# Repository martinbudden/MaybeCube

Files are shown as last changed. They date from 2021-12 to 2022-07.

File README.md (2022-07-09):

# MaybeCube

The **MaybeCube** is a fully-featured, rigid, high speed, and affordable CoreXY 3D printer with a linear rails motion system.

It can be built in a variety of sizes: the standard size is the MC350, which has external dimensions of approximately
405mm by 475mm by 415mm and a build volume of approximately 225mm x 225mm x 200mm.

The self-sourcing BOM cost of the MC300 variant is approximately £430 with a genuine E3D hotend (or about £400 with a generic
E3D compatible hotend), this does not include the cost of filament for printing parts, see [spreadsheet](documents/BOM_MC300.ods).
The MC350 variant is slightly more expensive.

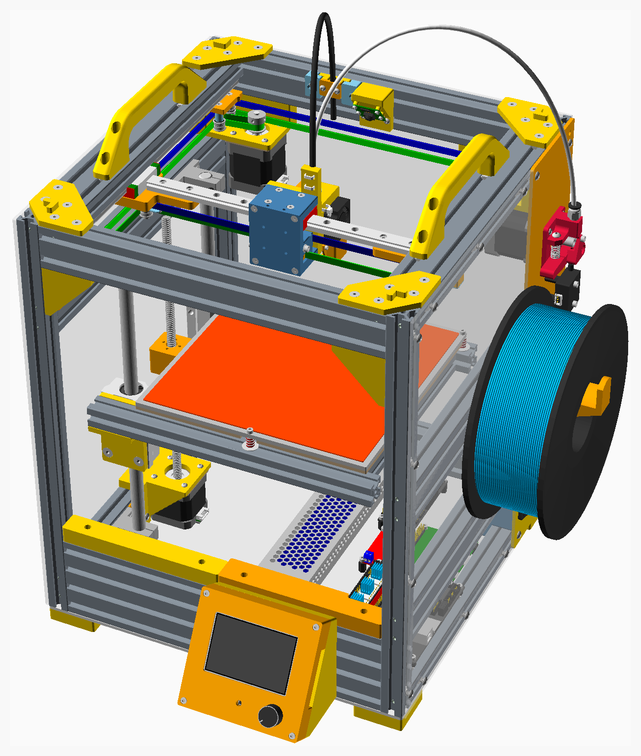
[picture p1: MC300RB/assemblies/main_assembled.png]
Main Assembly


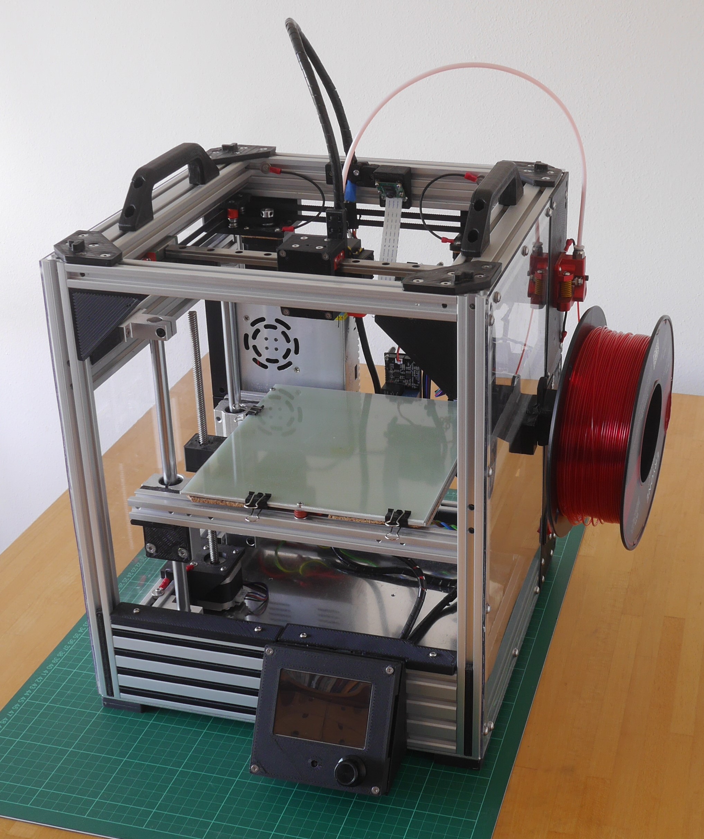
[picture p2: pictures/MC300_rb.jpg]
MaybeCube300


## Assembly instructions

The "standard" size is the MC350 variant. I have built the MC300 variant for two reasons: to test sizing (if the components
fit in the MC300 variant, then they will fit in larger variants); and because I had a quantity of 300mm extrusion and the
right size heated bed from an earlier project.

The assembly instructions and the BOM (parts list) for the MC300 variant are [here](https://github.com/martinbudden/MaybeCube/blob/main/MC300RB/readme.md).

The assembly instructions and the BOM for the MC350 variant are [here](https://github.com/martinbudden/MaybeCube/blob/main/MC350/readme.md).

Please read all the build instructions before you begin assembly.

The STL files are on [thingiverse](https://www.thingiverse.com/thing:4912095).

The assembly of the different MC300 and MC350 variants is essentially the same, the main differences are in the printbed.
Larger variants have a larger printbed and to support this can optionally have either Z-rods on both sides of the printbed,
or a 3-point kinematic bed.

If you would like to build a smaller printer, you may be interested in the MaybeCube's smaller sibling, the [BabyCube](https://github.com/martinbudden/BabyCube).

## Design Goals

1. **Create a high quality engineered 3D printer capable of producing high quality prints**
2. **Make the MaybeCube more easily usable in home environment (as opposed to garage or workshop)**
     * try and make it easy to transport and store the MaybeCube, so:
     * integrated design, everything is enclosed within the printer's frame with. This includes the motors,
       the motion system, the power supply, and the circuit boards. The only exceptions are the spool
       holder, which can be removed for transport and storage, and the extruder.
     * include base plate so underside of printer is not exposed
     * all protrusions from frame (filament spool, extruder, power connector) are on the right hand side to minimise desk
       clutter and allow the back of the MaybeCube to be pushed right against a wall
     * all protrusions from the frame can be easily removed for storage
     * clean wiring - route wiring in extrusion channels where possible and minimise exposed wiring
3. **Improve ease of assembly**
     * Use internal blind joints on the frame
     * printed parts designed so that bolts are accessible and can be tightened when frame fully assembled (that is bolt
       holes are not blocked by other parts when assembled)
     * divide the main assembly into a number of independent sub-assemblies.
     * where possible printed parts push up right against frame and so "auto-align"
     * facilitate building in different size variants
4. **Use linear rails for the x and y axes**
     * linear rails are now not much more expensive than linear rods
     * linear rails make design and assembly easier, reducing the need for custom printed parts
     * linear rods are used for the z-axis, since linear rails offer no advantage here
5. **Maximise frame rigidity**
     * one of my goals is to experiment with high print speeds. A highly rigid frame allows higher acceleration settings
     * use 2040 aluminium extrusion, corner joints are about 4 times more rigid than 2020 corner joints and 2-3 times more
       rigid than 3030 corner joints
6. **Maximise build volume for selected extrusion lengths**
     * Z-axis assembly is on the left side of MaybeCube. This means the Z-axis assembly does not impede travel in the Y direction
     * The printhead is quite compact, so does not significantly restrict travel in the X and Y directions
7. **Enable a fully enclosed print volume**
     * The cubic shape makes enclosure straightforward.
     * A panel can be used to isolate the electronics and stepper motors from the build volume
     * A slide-in front panel can be added
     * A top enclosure can be placed on the frame
8. **Try and keep the costs down**
     * the aim is not to be as cheap as possible, but rather to avoid unnecessary costs
     * use standard extrusions lengths, as far as possible, so no custom cutting is required
9. **Facilitate customisation and experimentation**
     * Open source design
     * Parametric design in OpenSCAD
     * The open design of the frame and the easy accessibility of parts means the MaybeCube is fairly easy to customise -
       most parts can be changed without the need to disassemble large parts of the frame
     * The design of the X_Carriage means it is easy to customise to support different hotends and extruders
     * Support other printhead systems, including EVA, XChange, and, in principle, the Jubilee and E3D toolchangers
     * The independence of the XY motion system and the Z motion system means that in principle the Z motion system could
       be replaced (with, say, an auto-tramming 3-point leveling system)

## Variations

The canonical form is the MC350 variant.

variant | Extrusion lengths | Rail/rod lengths | Approx Build Volume | Bed Size   | Exterior Dimensions
------- | ----------------- | ---------------- | ------------------- | ---------- | -------------------
MC250   | x250 y250 z350    | x200 y250 z250   | concept variant     | 180mm      | 290 x 290 x 350
MC300   | x300 y300 z400    | x250 y300 z300   | 185 x 185 x 200     | 214mm      | 340 x 340 x 400
MC350   | x350 y350 y400    | x300 y350 z300   | 225 x 225 x 200     | 235mm      | 390 x 390 x 400
MC400   | x400 y400 y500    | x350 y400 z400   | 275 x 275 x 300     | 310mm      | 440 x 440 x 450

## Comparisons

The following table compares the sizes and build volumes of various CoreXY 3D printers.

Printer           | EType | Extrusion lengths | Build Volume     | Exterior Dimensions
------------------|------ | ----------------- | ---------------- | -------------------
MC300             | 2040  | 300 x 300 x 400   | 185 x 185 x 200  | 340 x 340 x 420
MC350             | 2040  | 350 x 350 x 400   | 225 x 225 x 200  | 390 x 390 x 420
MC400             | 2040  | 400 x 400 x 500   | 275 x 275 x 300  | 440 x 440 x 520
MC450             | 2040  | 450 x 450 x 550   | 325 x 325 x 350  | 490 x 490 x 570
[BLV MGN Cube](https://www.blvprojects.com/blv-mgn-cube-3d-printer) | 2040 | 496 x 496 x 560 | 300 x 300 x 365 | 576 x 536 x 560
[Denali 200](https://github.com/Annex-Engineering/Denali) | 2020 | 320 x 320 x 590 | 200 x 200 x 200 | 380 x 380 x 620 (est)
Denali 250 | 2020 | 370 x 370 x 590 | 250 x 250 x 200 | 430 x 430 x 620 (est)
Denali 350 | 2020 | 470 x 470 x 690 | 350 x 350 x 300 | 530 x 530 x 720 (est)
[E3D ToolChanger](https://e3d-online.com/pages/toolchanger) | 2040 | Z: 500 |  200 x 300 x 300  | 530 x 505 x 500
[FuseBox3](https://github.com/alexyu132/fusebox3) | 2020 | 310 x 332 x 407 | 235 x 235 x 235 | 350 x 372 x 427
[HyperCube](https://www.thingiverse.com/thing:1752766) | 2020 | 340 x 303 x 350  | 200 x 200 x 155  | 380 x 343 x 350
[HEVO](https://www.thingiverse.com/thing:2254103) | 3030 | 420 x 410 x 500 | 300 x 300 x 300 | 480 x 470 x 500
[HevORT 315](https://miragec79.github.io/HevORT/) | 3030 | 410 x 420 x 880 | 315 x 315 x 340 | 640 x 480 x 890 (est)
HevORT 415                                        | 3030 | 510 x 520 x 980 | 415 x 415 x 440 | 740 x 480 x 990 (est)
[Jubilee](https://www.jubilee3d.com/index.php?title=Main_Page) | 2020 | 409 x 604 x 430 | 300 x 300 x 300 | 476 x 604 x 558
[RatRig V-Core3 300](https://v-core.ratrig.com/#customization) | 3030 | 440 x 505 x 510 | 300 x 300 x 300  | 518 x 583 x 560
RatRig V-Core3 400 | 3030 | 540 x 605 x 610 | 400 x 400 x 400  | 618 x 683 x 660
RatRig V-Core3 500 | 3030 | 640 x 705 x 710 | 500 x 500 x 500  | 718 x 783 x 760
[RailCore II 300ZL](https://railcore.org/) | 1515 | 400 x 370 x 360 | 250 x 250 x 280 | 522 x 445 x 496
RailCore II 300ZL  | 1515 | 460 x 425 x 445 | 300 x 300 x 330 | 572 x 495 x 546
RailCore II 300ZLT | 1515 | 460 x 425 x 745 | 300 x 300 x 600 | 572 x 495 x 830
[SimpleCore 200](https://github.com/rolohaun/SimpleCore) | 2020 | 350 x 350 x 450 | 200 x 200 x 180 | 390 x 390 x 390 (est)
SimpleCore 300 | 2020 | 500 x 500 x 500 | 330 x 330 x 230 | 540 x 540 x 540 (est)
[SnakeOil XY 180](https://github.com/ChipCE/SnakeOil-XY) | 3030 | 310 x 310 x 500 | 180 x 180 x 180 | 400 x 390 x 520 (est)
SnakeOil XY 250 | 3030 | 400 x 370 x 550 | 250 x 240 x 230 | 490 x 450 x 570 (est)
[Ultra MegaMax Dominator](https://drmrehorst.blogspot.com/2017/07/ultra-megamax-dominator-3d-printer.html) | 4040 | | 300 x 300 x 695 | 610 x 530 x 1500
[Voron 0](https://vorondesign.com/voron0) | 1515 | 200 x 200 x 200 | 120 x 120 x 120 | 230 x 230 x 280
[Voron2 v2.4 250](https://vorondesign.com/voron2.4) | 2020 | 410 x 410 x 430 | 250 x 250 x 230 | 450 x 450 x 430
Voron2 v2.4 300    | 2020 | 460 x 460 x 480 | 300 x 300 x 280 | 500 x 500 x 480
Voron2 v2.4 350    | 2020 | 510 x 510 x 530 | 350 x 350 x 330 | 550 x 550 x 530
[VzBot](https://github.com/VzBot3D/VzBot) | 2020/2040 | 530 x 460 x 530 | 330 x 330 x 400 | 530 x 500 x 570

## Frame stiffness

The MaybeCube is a cuboid with 6 rectangular faces. Rectangles have no inherent rigidity and are subject to shearing. The
rigidity of a rectangle is provided solely by the strength of its joints, and these often do not provide sufficient rigidity.
A small movement at a joint is magnified into a much larger movement at the end of a 400mm extrusion.
There are three main ways to increase the rigidity of rectangles:

1. triangulation, where the a diagonal piece divides the rectangle into two triangles, this is exemplified in [truss bridges](https://en.wikipedia.org/wiki/Truss_bridge)
2. using a shear plate, this is exemplified in the [sheer boards](https://en.wikipedia.org/wiki/Shear_wall) used to stiffen
   wooden framed buildings
3. reinforcing the joints.

The MaybeCube uses 2040 extrusions, these provide significantly more joint rigidity than either 2020 or 3030 extrusions.
Additionally the MaybeCube uses shear plates on the bottom, back, and (optionally) left and right faces to stiffen the frame.

The front face of the MaybeCube is the most subject to shearing, since it needs to be open to allow access to the printbed.
Two measures are taken to counteract this: 2080 rather than 2040 extrusion is used at the bottom of the face, and the idler
mounts at the top are extended to provide some triangulation and reinforcement of the upper joints.

## Input shaper test results (MC300 variant with side panels)

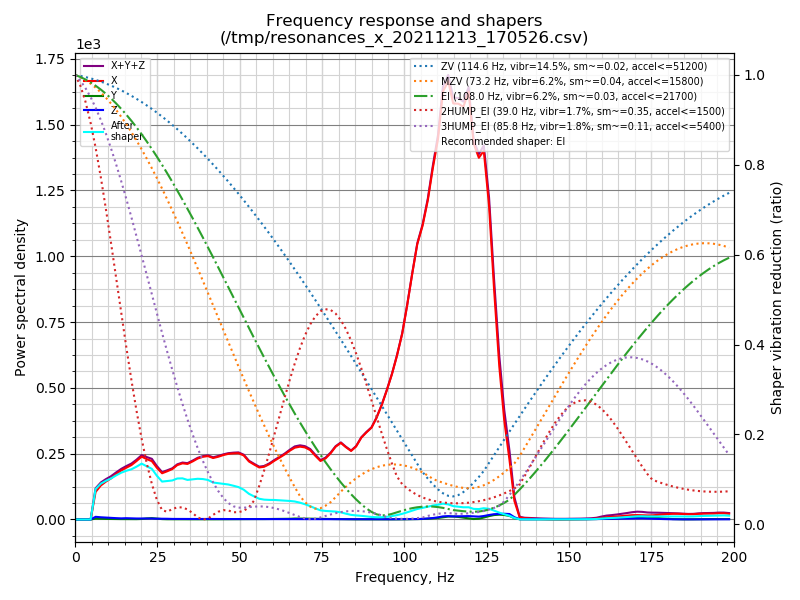
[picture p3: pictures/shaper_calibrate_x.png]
X-Axis

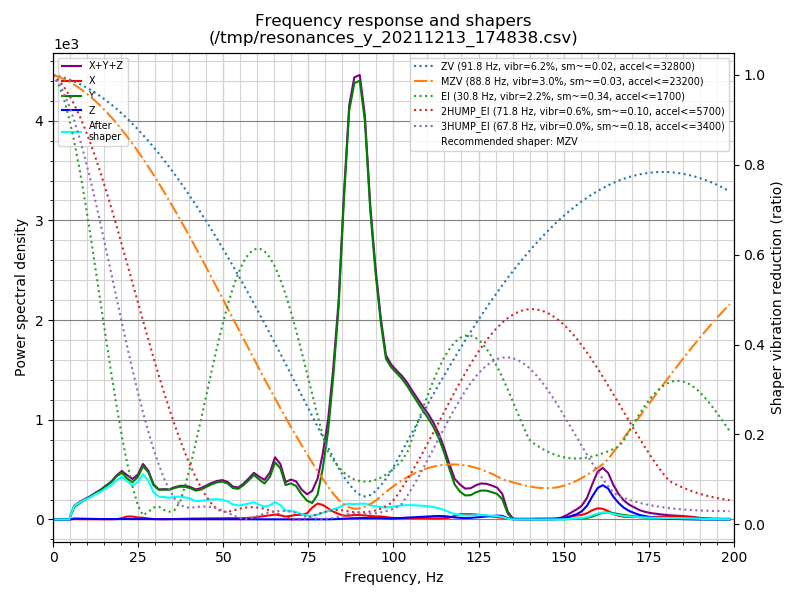
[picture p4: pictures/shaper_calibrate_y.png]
Y-Axis


### Comparison of input shaper test results

Printer                                                    | X frequency | X amplitude | X acc limit | Y frequency | Y amplitude | Y acc limit
---------------------------------------------------------- | ----------- | ----------- | ------------| ----------- | ----------- | -----------
MC300                                                      |         114 |       1,720 |      51,200 |          88 |       4,500 | 32,800
[BabyCube](https://github.com/martinbudden/BabyCube)       |          92 |      19,000 |      32,600 |          87 |      13,500 | 44,100
[RatRig V-Core3 300](https://youtu.be/ZAN9zTTPUq8?t=765)   |          62 |      47,500 |      15,300 |         N/A |         N/A | N/A
[SnakeOil XY](https://github.com/ChipCE/SnakeOil-XY)       |          83 |     110,000 |      27,400 |          56 |      49,500 | 12,100
[VzBot](https://youtu.be/hTF4bWBTqDQ?t=298)                |          93 |      87,000 |      34,100 |          64 |      35,500 | 15,900
[Voron 2.4](https://youtu.be/a775O9luKgA?t=7100)           |     52 & 82 |      15,400 |      26,500 |     38 & 63 |      11,600 |  9,900
[Voron Switchwire](https://youtu.be/OoWQUcFimX8?t=635)     |          70 |      11,000 |         N/A |          48 |      16,200 | N/A
[Ender 3](https://www.youmaketech.com/klipper-on-ender-3/) |     30 & 88 |       4,100 |       3,800 |     32 & 57 |      19,000 |  9,300
[Prusa i3 MKS+](https://forum.prusaprinters.org/forum/original-prusa-i3-mk3s-mk3-general-discussion-announcements-and-releases/prusa-i3-mks3-resonance-profiles-input-shaper/) | 38 & 58 | 39,000 | N/A | 32 & 78 | 42,000 | N/A

These input shaper results give a rough idea of the rigidity of various printers. The acc limit is the value of the max
acceleration for the ZV shaper for each printer and axis - it is not that meaningful in itself, but it does form some
basis for comparison.

It does seem that the MC300 compares very favourably with the other printers for which I have found results published.

## Customisations

### EVA module printhead system (version 2.4.2)

In its default configuration the MaybeCube has an E3D V6 hotend with a Bowden extruder. However I've created adaptors
so that the [EVA modular printhead system](https://main.eva-3d.page) can be used. The EVA system supports a wide variety
of hotends and extruders. More details on using the EVA adaptors are [here](https://github.com/martinbudden/MaybeCube/tree/main/EVA_2_4_2).

The STL files are on [thingiverse](https://www.thingiverse.com/thing:4912099).

In the picture below, EVA adaptors are printed in blue, MaybeCube standard parts are printed in red, and EVA standard parts
are printed in black and green.

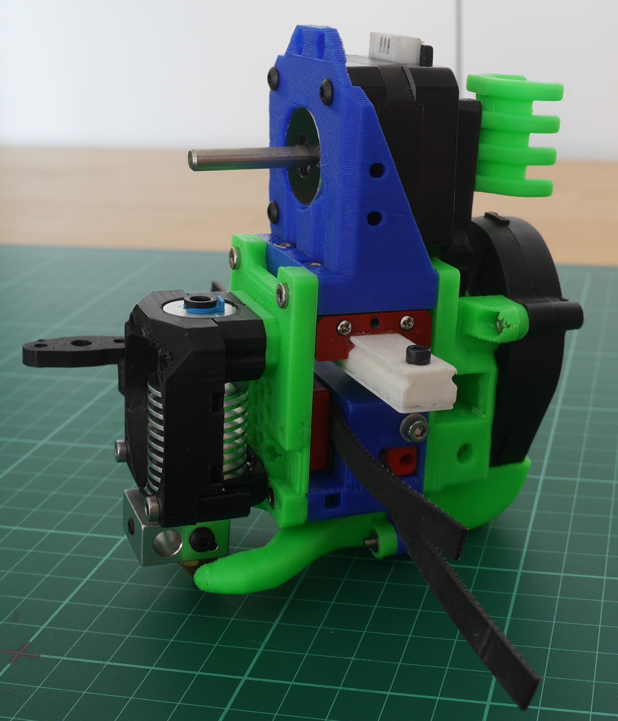
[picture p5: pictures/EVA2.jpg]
EVA2


### Printermods XChange quick change tool head

I've created an adaptor for the
[Printermods XChange quick change tool head](https://www.kickstarter.com/projects/printermods/xchange-v10-hot-swap-tool-changing-for-every-3d-printer).
More details on using the XChange adaptor are [here](https://github.com/martinbudden/MaybeCube/tree/main/XChange).

The STL files are on [thingiverse](https://www.thingiverse.com/thing:4924355).

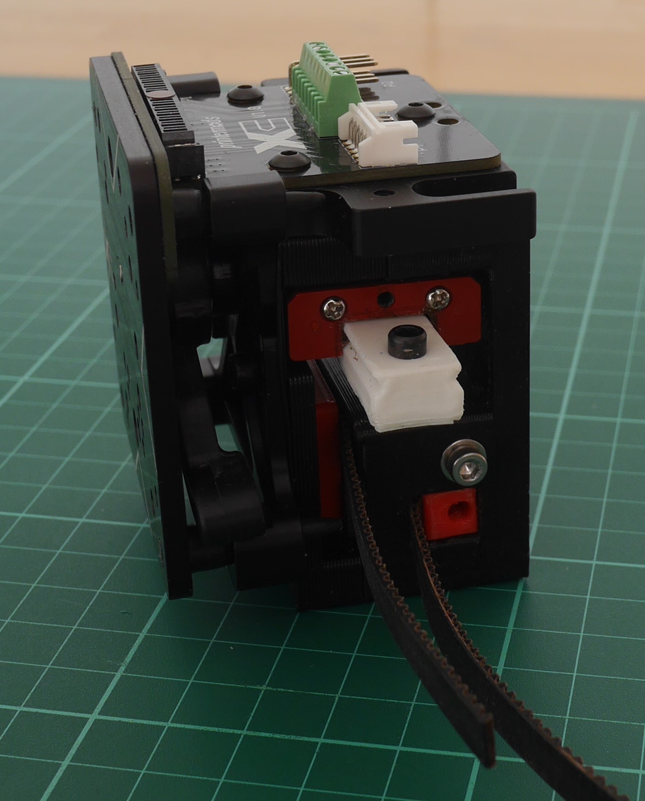
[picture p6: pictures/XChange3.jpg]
XChange


### Voron Mini Afterburner printhead

I've created an adaptor for the Voron Mini Afterburner (as used on the [Voron V0](https://github.com/VoronDesign/Voron-0))
printhead.

More details on using the Voron Mini Afterburner adaptor are [here](https://github.com/martinbudden/MaybeCube/tree/main/Voron_Mini_Afterburner).

The STL file is [here](https://github.com/martinbudden/MaybeCube/blob/main/Voron_Mini_Afterburner/stls/X_Carriage_Voron_Mini_Afterburner.stl).

### E3D tool changer

Currently there is no adaptor for the  [E3D tool changer](https://e3d-online.com/pages/toolchanger), however I think it
would be fairly straightforward to create one.

There should be room to dock at least two, and perhaps three [E3D ToolChanger Tools](https://e3d-online.com/products/toolchanger-tools)
in the back of the MC350, this would allow experimenting with the E3D docking system in a framework considerably less
expensive than the [E3D Motion System](https://e3d-online.com/products/e3d-motion-system).

### Jubilee tool changer

The [Jubilee 3D printer](https://www.jubilee3d.com/index.php?title=Main_Page)
has a [tool changer](https://www.jubilee3d.com/index.php?title=Tools)
compatible with the E3D tool changer. I have a proof of concept showing that this tool changer system can be used on the
MaybeCube. Note that this is incomplete and still requires an X_Carriage adaptor for the Jubilee plates.

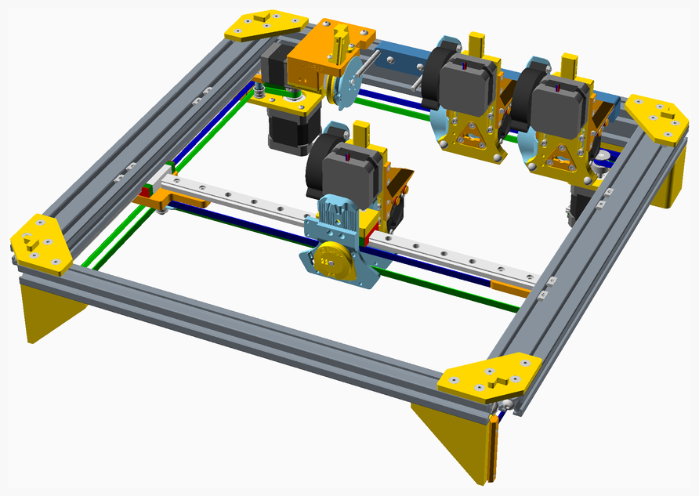
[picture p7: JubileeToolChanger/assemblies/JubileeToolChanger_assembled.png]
JubileeToolChanger Assembly


### 3-point Kinematic Bed

The MC300 and MC350 use a cantilevered print bed. For larger variants a 3-point Kinematic Bed is recommended.

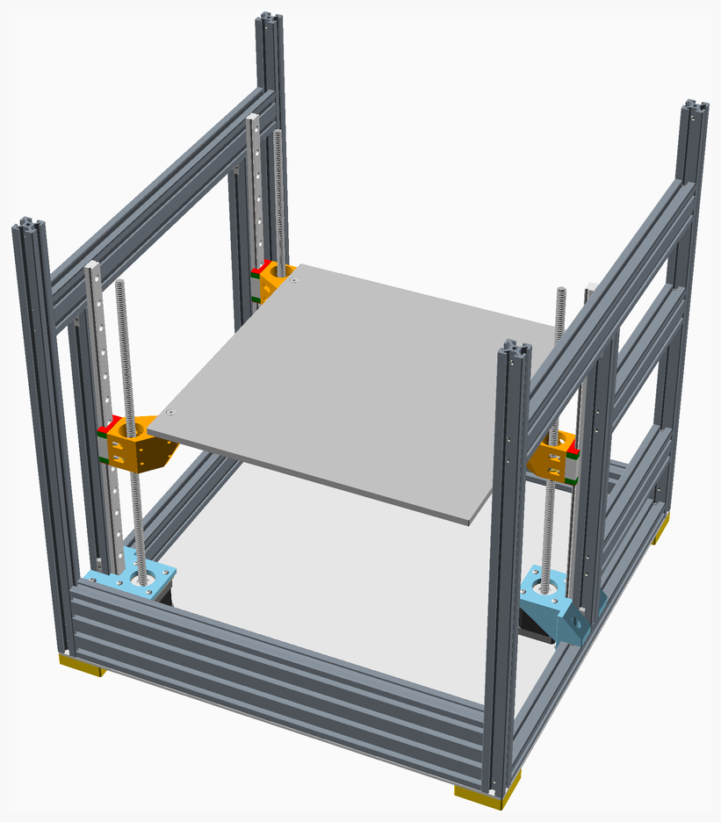
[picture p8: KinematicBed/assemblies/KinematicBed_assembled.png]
KinematicBed Assembly


### Dual Z rods

Alternatively, for larger variants,  it is possible to use dual sets of Z-rods to support the print bed.

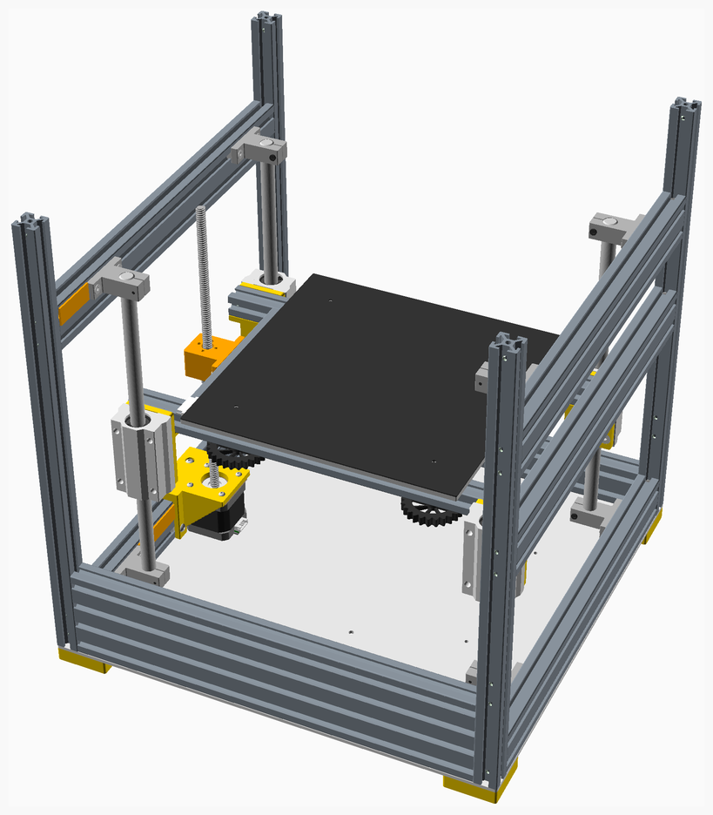
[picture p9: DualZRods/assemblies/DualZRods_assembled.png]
DualZRods Assembly


## Pictures

In these pictures the power supply and PCBs are mounted in the back of the printer - I've done this in the development build
so that I can easily change things around while I experiment. For the release build, the power supply and PCBs are mounted
in the base of the printer.

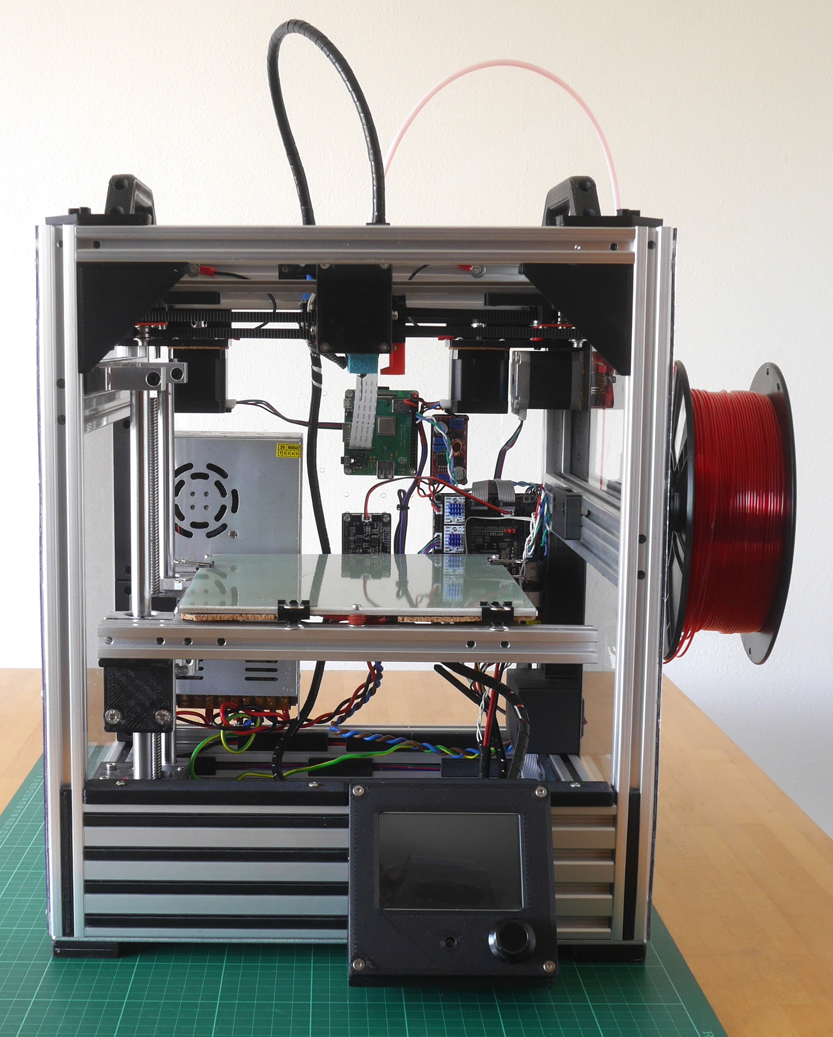
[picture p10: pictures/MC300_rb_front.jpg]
Front

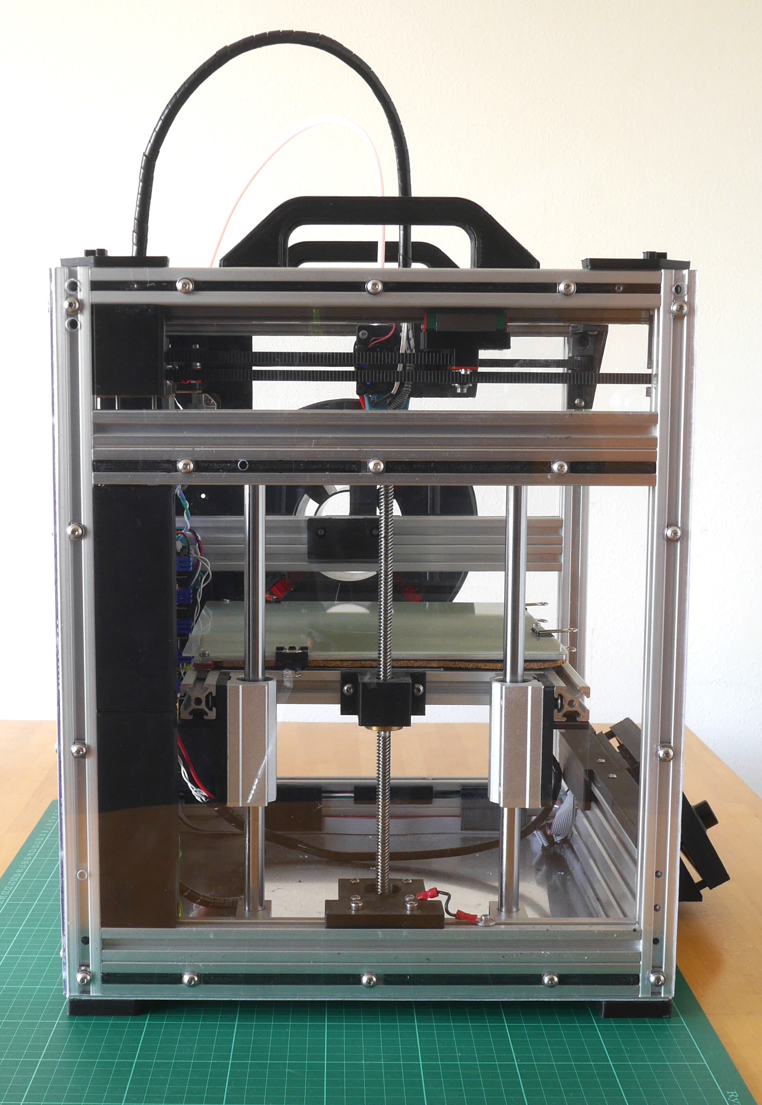
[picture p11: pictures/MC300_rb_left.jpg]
Left

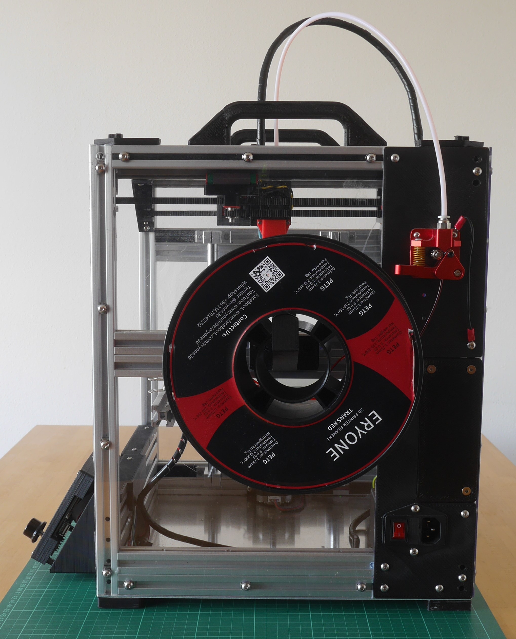
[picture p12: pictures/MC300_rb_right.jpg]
Right

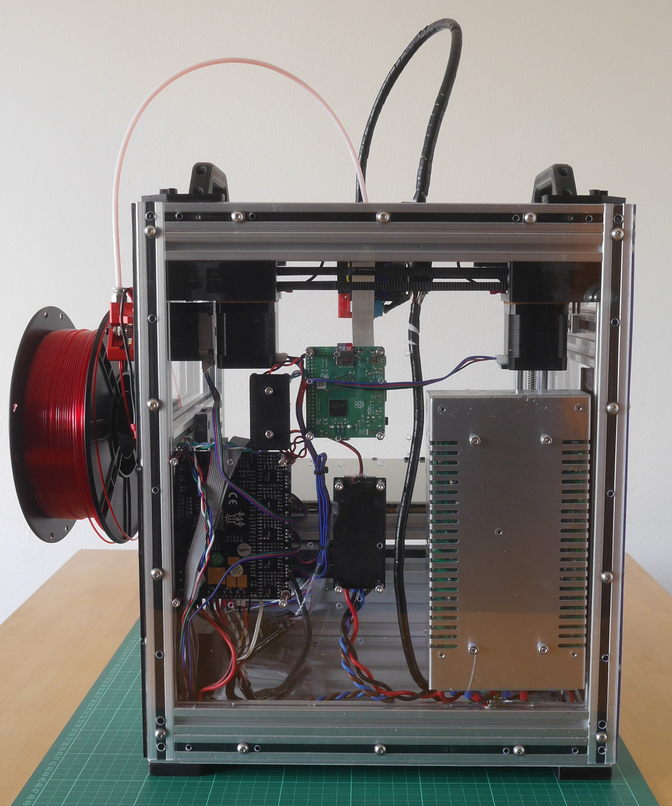
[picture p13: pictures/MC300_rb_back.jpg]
Back


## License

MaybeCube is licensed under the [Creative Commons Attribution-NonCommercial-ShareAlike 4.0 International License](https://creativecommons.org/licenses/by-nc-sa/4.0/)
(CC BY-NC-SA 4.0)<br />
<a rel="license" href="http://creativecommons.org/licenses/by-nc-sa/4.0/">

</a>

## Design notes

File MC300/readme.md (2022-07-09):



# MaybeCube Assembly Instructions

# OUTDATED MaybeCube Assembly Instructions OUTDATED

**THIS VARIANT HAS BEEN SUPERSEDED BY THE VARIANT [HERE](https://github.com/martinbudden/MaybeCube/blob/main/MC300RB/readme.md).**

**THESE INSTRUCTIONS HAVE BEEN KEPT FOR HISTORICAL REASONS.**

These are the assembly instructions for the MaybeCube. These instructions are not fully comprehensive, that is they do
not show every small detail of the construction and in particular they do not show the wiring. However there is sufficient
detail that someone with a good understanding of 3D printers can build the MaybeCube.

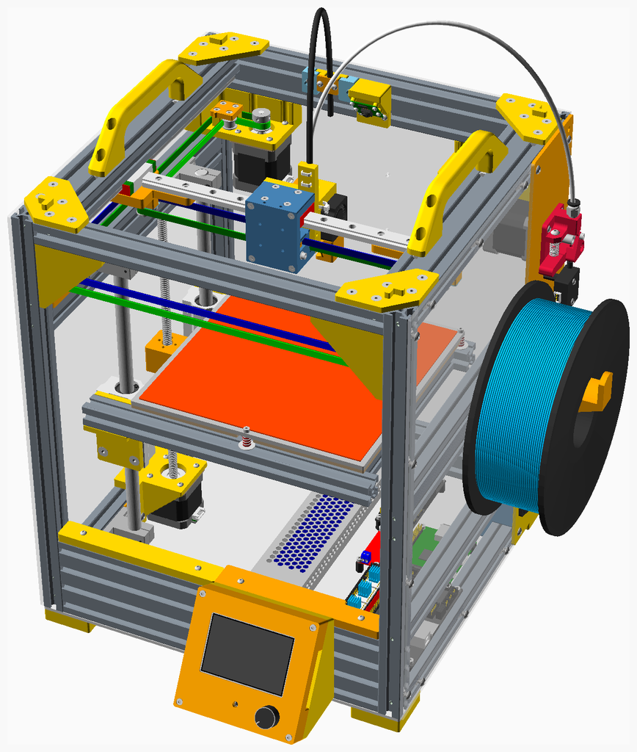
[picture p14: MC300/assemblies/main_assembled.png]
Main Assembly


## Printing the parts

A number of parts are in proximity with heat sources, namely the hotend, the heated bed and the motors. Ideally these should be
printed in ABS, but I have used PETG successfully. These parts are insulated from direct contact with the heat sources, by
cork underlay (for the heated bed) and by cork dampers (for the motors). These insulators should not be omitted from the build.

<span></span>

---

## Table of Contents

1. [Parts list](#Parts_list)
1. [Printhead_E3DV6 assembly](#Printhead_E3DV6_assembly)
1. [X_Carriage_Belt_Side assembly](#X_Carriage_Belt_Side_assembly)
1. [XY_Motor_Mount_Right assembly](#XY_Motor_Mount_Right_assembly)
1. [XY_Motor_Mount_Left assembly](#XY_Motor_Mount_Left_assembly)
1. [XY_Idler_Right assembly](#XY_Idler_Right_assembly)
1. [XY_Idler_Left assembly](#XY_Idler_Left_assembly)
1. [Y_Carriage_Right assembly](#Y_Carriage_Right_assembly)
1. [Right_Side_Upper_Extrusion assembly](#Right_Side_Upper_Extrusion_assembly)
1. [Y_Carriage_Left assembly](#Y_Carriage_Left_assembly)
1. [Left_Side_Upper_Extrusion assembly](#Left_Side_Upper_Extrusion_assembly)
1. [Face_Top_Stage_1 assembly](#Face_Top_Stage_1_assembly)
1. [Face_Top_Stage_2 assembly](#Face_Top_Stage_2_assembly)
1. [Face_Top assembly](#Face_Top_assembly)
1. [Extruder_Bracket assembly](#Extruder_Bracket_assembly)
1. [Right_Side assembly](#Right_Side_assembly)
1. [Display_Cover_TFT35_E3 assembly](#Display_Cover_TFT35_E3_assembly)
1. [IEC_Housing assembly](#IEC_Housing_assembly)
1. [Base_Plate_Stage_1 assembly](#Base_Plate_Stage_1_assembly)
1. [Base_Plate assembly](#Base_Plate_assembly)
1. [Heated_Bed assembly](#Heated_Bed_assembly)
1. [Z_Carriage_Side assembly](#Z_Carriage_Side_assembly)
1. [Z_Carriage_Center assembly](#Z_Carriage_Center_assembly)
1. [Printbed_Frame assembly](#Printbed_Frame_assembly)
1. [Printbed_Frame_with_Z_Carriages assembly](#Printbed_Frame_with_Z_Carriages_assembly)
1. [Printbed assembly](#Printbed_assembly)
1. [Left_Side assembly](#Left_Side_assembly)
1. [Left_Side_with_Printbed assembly](#Left_Side_with_Printbed_assembly)
1. [Stage_1 assembly](#Stage_1_assembly)
1. [Stage_2 assembly](#Stage_2_assembly)
1. [Stage_3 assembly](#Stage_3_assembly)
1. [Stage_4 assembly](#Stage_4_assembly)
1. [Main assembly](#main_assembly)

<span></span>
[Top](#TOP)

---

## Parts list

| <span style="writing-mode: vertical-rl; text-orientation: mixed;">Printhead E3DV6</span> | <span style="writing-mode: vertical-rl; text-orientation: mixed;">X Carriage Belt Side</span> | <span style="writing-mode: vertical-rl; text-orientation: mixed;">Face Top</span> | <span style="writing-mode: vertical-rl; text-orientation: mixed;">Right Side</span> | <span style="writing-mode: vertical-rl; text-orientation: mixed;">Heated Bed</span> | <span style="writing-mode: vertical-rl; text-orientation: mixed;">Printbed</span> | <span style="writing-mode: vertical-rl; text-orientation: mixed;">Left Side</span> | <span style="writing-mode: vertical-rl; text-orientation: mixed;">Main</span> | <span style="writing-mode: vertical-rl; text-orientation: mixed;">TOTALS</span> |  |
|-----:|-----:|-----:|-----:|-----:|-----:|-----:|-----:|---:|:---|
| | | | | | | | | | **Vitamins** |
| .  | .  | .  | .  | .  | .  | .  | 1  | 1  |  Aluminium sheet 340mm x 340mm x 3mm |
| .  | .  | 1  | .  | .  | .  | .  | .  | 1  |  Belt GT2 x 6mm x 1260mm |
| .  | .  | 1  | .  | .  | .  | .  | .  | 1  |  Belt GT2 x 6mm x 1270mm |
| .  | .  | .  | .  | .  | .  | .  | 1  | 1  |  BigTreeTech Relay Module v1.2 |
| .  | .  | .  | .  | .  | .  | .  | 1  | 1  |  BigTreeTech SKR v1.4 Turbo |
| .  | .  | .  | .  | .  | .  | .  | 1  | 1  |  BigTreeTech TFT35 E3 v3.0 |
| 4  | .  | .  | .  | .  | .  | .  | .  | 4  |  Bolt M2 caphead x  6mm |
| .  | .  | 4  | .  | .  | .  | .  | .  | 4  |  Bolt M2 caphead x  8mm |
| .  | .  | .  | .  | .  | 2  | .  | 2  | 4  |  Bolt M3 buttonhead x  8mm |
| .  | .  | 2  | .  | .  | .  | .  |  16  | 18  |  Bolt M3 buttonhead x 10mm |
| .  | .  | 8  | .  | .  | .  | .  | 8  | 16  |  Bolt M3 buttonhead x 12mm |
| .  | .  | .  | 2  | .  | .  | .  | .  | 2  |  Bolt M3 buttonhead x 16mm |
| .  | .  | .  | .  | .  | .  | .  |  20  | 20  |  Bolt M3 caphead x  6mm |
| .  | .  |  32  | .  | .  | 4  | .  | .  | 36  |  Bolt M3 caphead x 10mm |
| .  | .  | 2  | .  | .  | .  | .  | .  | 2  |  Bolt M3 caphead x 16mm |
| .  | .  | .  | .  | 3  | .  | .  | .  | 3  |  Bolt M3 caphead x 20mm |
| .  | .  | 2  | .  | .  | .  | .  | 4  | 6  |  Bolt M3 caphead x 25mm |
| .  | .  | 2  | .  | .  | .  | .  | .  | 2  |  Bolt M3 caphead x 30mm |
| .  | 2  | .  | .  | .  | .  | .  | .  | 2  |  Bolt M3 caphead x 40mm |
| .  | .  | .  | 2  | .  | .  | .  | .  | 2  |  Bolt M3 countersunk x  8mm |
| .  | .  | 2  | .  | .  | 2  | .  | .  | 4  |  Bolt M3 countersunk x 10mm |
| .  | .  | 4  | .  | .  | .  | .  | .  | 4  |  Bolt M3 countersunk x 12mm |
| 2  | .  | 8  | .  | .  | .  | .  | .  | 10  |  Bolt M3 countersunk x 25mm |
| .  | .  | .  | .  | .  | .  | .  | 4  | 4  |  Bolt M3 countersunk x 40mm |
| .  | .  | .  | 9  | .  | .  | .  |  38  | 47  |  Bolt M4 buttonhead x  8mm |
| .  | .  |  16  | .  | .  | 6  | 2  |  14  | 38  |  Bolt M4 buttonhead x 10mm |
| .  | .  | 8  | .  | .  | .  | 2  | 4  | 14  |  Bolt M4 buttonhead x 12mm |
| .  | .  | .  | .  | .  | .  | .  |  14  | 14  |  Bolt M4 countersunk x  8mm |
| .  | .  |  20  | .  | .  | .  | 8  | .  | 28  |  Bolt M4 countersunk x 10mm |
| .  | .  | 4  | .  | .  | .  | .  | .  | 4  |  Bolt M5 buttonhead x 10mm |
| .  | .  |  10  | 6  | .  | 8  | 8  |  14  | 46  |  Bolt M5 buttonhead x 12mm |
| .  | .  | .  | .  | .  | 4  | .  | .  | 4  |  Bolt M5 buttonhead x 16mm |
| .  | .  | .  | .  | .  | 4  | .  | .  | 4  |  Bolt M5 countersunk x 12mm |
| .  | .  | 2  | 1  | .  | .  | .  | 1  | 4  |  Cork damper NEMA 17 |
| .  | .  | .  | .  | .  | 1  | .  | .  | 1  |  Cork underlay 214mm x 214mm |
| .  | .  | .  | .  | .  | 2  | .  | .  | 2  |  Extrusion E2020 x 265mm |
| .  | .  | 1  | 1  | .  | .  | .  | 1  | 3  |  Extrusion E2020 x 300mm |
| .  | .  | .  | 2  | .  | .  | 2  | .  | 4  |  Extrusion E2020 x 400mm |
| .  | .  | .  | .  | .  | 2  | .  | .  | 2  |  Extrusion E2040 x 188mm |
| .  | .  | 3  | 1  | .  | .  | 2  | 1  | 7  |  Extrusion E2040 x 300mm |
| .  | .  | .  | .  | .  | .  | .  | 1  | 1  |  Extrusion E2080 x 300mm |
| 1  | .  | .  | .  | .  | .  | .  | .  | 1  |  Fan 30mm x 10mm |
| .  | .  | .  | 1  | .  | .  | .  | .  | 1  |  Filament sensor |
| .  | .  | .  | .  | 1  | .  | .  | .  | 1  |  Heated Bed 214mm x 214mm |
| .  | .  | 4  | .  | .  | .  | .  | .  | 4  |  Heatfit insert M3 |
| 1  | .  | .  | .  | .  | .  | .  | .  | 1  |  Hot end E3D V6 direct 1.75mm |
| .  | .  | .  | .  | .  | .  | .  | 1  | 1  |  IEC320 C14 switched fused inlet module |
| .  | .  | .  | .  | .  | 1  | .  | .  | 1  |  Leadscrew nut 8 x 2 |
| .  | .  | 1  | .  | .  | .  | .  | .  | 1  |  Linear rail MGN12 x 250mm |
| .  | .  | 2  | .  | .  | .  | .  | .  | 2  |  Linear rail MGN12 x 300mm |
| .  | .  | 3  | .  | .  | .  | .  | .  | 3  |  Linear rail carriage MGN12H |
| .  | .  | .  | .  | .  | .  | .  | 2  | 2  |  Linear rod 12mm x 300mm |
| .  | .  | .  | 1  | .  | .  | .  | .  | 1  |  MK10 Dual Pulley Extruder |
| .  | .  | .  | .  | .  | .  | .  | 1  | 1  |  Micro SD card |
| .  | .  |  18  | .  | 3  | 2  | .  | 4  | 27  |  Nut M3 hammer |
| .  | .  |  10  | 8  | .  | .  | .  |  66  | 84  |  Nut M4 hammer |
| .  | .  |  36  | .  | .  | 6  |  12  | .  | 54  |  Nut M4 sliding T |
| .  | .  | .  | .  |  12  | .  | .  | .  | 12  |  O-ring nitrile 4mm x 2mm |
| .  | .  | .  | .  | .  | .  | .  | 1  | 1  |  PSU NIUGUY CB-500W-24V |
| .  | .  | .  | .  | .  | .  | .  | 1  | 1  |  PTFE Bowden tube, 500 mm |
| .  | .  | .  | .  | .  | .  | .  |  12  | 12  |  Pillar hex nylon F/F M3x10 |
| .  | .  | .  | 2  | .  | .  | .  | .  | 2  |  Pillar hex nylon F/F M3x14 |
| .  | .  | .  | .  | .  | .  | .  | 4  | 4  |  Pillar hex nylon F/F M3x20 |
| .  | .  | 8  | .  | .  | .  | .  | .  | 8  |  Pulley GT2 idler 16 teeth |
| .  | .  | 4  | .  | .  | .  | .  | .  | 4  |  Pulley GT2 idler smooth 9.63mm |
| .  | .  | 2  | .  | .  | .  | .  | .  | 2  |  Pulley GT2OB 20 teeth |
| .  | .  | .  | .  | .  | .  | .  | 1  | 1  |  Raspberry Pi 3A+ |
| .  | .  | 1  | .  | .  | .  | .  | .  | 1  |  Raspberry Pi camera V2 |
| .  | .  | .  | .  | .  | 2  | .  | .  | 2  |  SCS12LUU bearing block |
| .  | .  | .  | .  | .  | .  | 4  | .  | 4  |  SK12 shaft support bracket |
| .  | .  | .  | .  | .  | .  | .  | 1  | 1  |  Sheet polycarbonate 250mm x 400mm x 3mm |
| .  | .  | .  | .  | .  | .  | .  | 2  | 2  |  Sheet polycarbonate 340mm x 400mm x 3mm |
| 1  | .  | .  | .  | .  | .  | .  | .  | 1  |  Square radial fan 3010 |
| .  | .  | .  | .  | .  | .  | .  | 1  | 1  |  Stepper motor NEMA17 x 40mm, 280mm integrated leadscrew |
| .  | .  | 2  | 1  | .  | .  | .  | .  | 3  |  Stepper motor NEMA17 x 47mm |
| .  | .  | .  | 1  | .  | .  | .  | .  | 1  |  Stepper motor cable, 200mm |
| .  | .  | 1  | .  | .  | .  | .  | .  | 1  |  Stepper motor cable, 300mm |
| .  | .  | 1  | .  | .  | .  | .  | .  | 1  |  Stepper motor cable, 500mm |
| .  | .  | .  | .  | .  | .  | .  | 1  | 1  |  Stepper motor cable, 750mm |
| .  | 2  |  26  | .  |  12  | .  | .  | .  | 40  |  Washer  M3 |
| .  | .  | 2  | .  | .  | .  | .  | .  | 2  |  Washer  M4 |
| .  | .  | .  | .  | 3  | .  | .  | .  | 3  |  Washer penny  M4 |
| .  | .  | .  | .  | .  | .  | .  | 1  | 1  |  XL4015 buck converter |
| 3  | .  | .  | .  | .  | .  | .  | .  | 3  |  Ziptie 2.5mm x 100mm min length |
|  12  | 4  | 253  |  38  |  34  |  46  |  40  | 245  |  672  | Total vitamins count |
| | | | | | | | | | **3D printed parts** |
| .  | .  | 1  | .  | .  | .  | .  | .  | 1  | Camera_Mount.stl |
| .  | .  | .  | .  | .  | .  | .  | 1  | 1  | Display_Housing_Bracket_TFT35_E3.stl |
| .  | .  | .  | .  | .  | .  | .  | 1  | 1  | Display_Housing_TFT35_E3.stl |
| .  | .  | .  | 1  | .  | .  | .  | .  | 1  | Extruder_Bracket.stl |
| 1  | .  | .  | .  | .  | .  | .  | .  | 1  | Fan_Duct.stl |
| .  | .  | .  | .  | .  | .  | .  | 4  | 4  | Foot_LShaped_12mm.stl |
| .  | .  | .  | .  | .  | .  | .  | 1  | 1  | Front_Cover_300.stl |
| .  | .  | .  | .  | .  | .  | .  | 1  | 1  | Front_Display_Wiring_Cover_300.stl |
| .  | .  | 2  | .  | .  | .  | .  | .  | 2  | Handle.stl |
| 1  | .  | .  | .  | .  | .  | .  | .  | 1  | Hotend_Clamp.stl |
| .  | .  | .  | .  | .  | .  | .  | 1  | 1  | IEC_Housing.stl |
| .  | .  | .  | .  | .  | .  | .  | 1  | 1  | IEC_Housing_Mount.stl |
| .  | .  | .  | .  | .  | 1  | .  | .  | 1  | Printbed_Strain_Relief.stl |
| .  | .  | .  | .  | .  | 1  | .  | .  | 1  | Printbed_Strain_Relief_Clamp.stl |
| .  | .  | .  | 1  | .  | .  | .  | .  | 1  | Right_Side_Panel.stl |
| .  | .  | .  | 1  | .  | .  | .  | .  | 1  | Right_Side_Panel_Bracket.stl |
| .  | .  | .  | .  | .  | .  | .  | 1  | 1  | Spool_Holder.stl |
| .  | .  | .  | .  | .  | .  | .  | 1  | 1  | Spool_Holder_36.stl |
| .  | .  | .  | .  | .  | .  | .  | 1  | 1  | Spool_Holder_Bracket.stl |
| .  | .  | 4  | .  | .  | .  | .  | .  | 4  | Top_Corner_Piece.stl |
| .  | .  | .  | .  | .  | .  | .  | 1  | 1  | Wiring_Guide.stl |
| .  | .  | .  | .  | .  | .  | .  | 1  | 1  | Wiring_Guide_Clamp.stl |
| .  | .  | 1  | .  | .  | .  | .  | .  | 1  | Wiring_Guide_Socket.stl |
| .  | .  | 2  | .  | .  | .  | .  | .  | 2  | XY_Idler_Channel_Nut.stl |
| .  | .  | 1  | .  | .  | .  | .  | .  | 1  | XY_Idler_Left_16.stl |
| .  | .  | 1  | .  | .  | .  | .  | .  | 1  | XY_Idler_Right_16.stl |
| .  | .  | 1  | .  | .  | .  | .  | .  | 1  | XY_Motor_Mount_Brace_Left_16.stl |
| .  | .  | 1  | .  | .  | .  | .  | .  | 1  | XY_Motor_Mount_Brace_Right_16.stl |
| .  | .  | 1  | .  | .  | .  | .  | .  | 1  | XY_Motor_Mount_Left_16.stl |
| .  | .  | 1  | .  | .  | .  | .  | .  | 1  | XY_Motor_Mount_Right_16.stl |
| .  | .  | 1  | .  | .  | .  | .  | .  | 1  | X_Carriage_Belt_Clamp.stl |
| .  | 1  | .  | .  | .  | .  | .  | .  | 1  | X_Carriage_Belt_Side_16.stl |
| .  | 2  | .  | .  | .  | .  | .  | .  | 2  | X_Carriage_Belt_Tensioner.stl |
| 1  | .  | .  | .  | .  | .  | .  | .  | 1  | X_Carriage_Groovemount.stl |
| .  | .  | 1  | .  | .  | .  | .  | .  | 1  | Y_Carriage_Brace_Left_16.stl |
| .  | .  | 1  | .  | .  | .  | .  | .  | 1  | Y_Carriage_Brace_Right_16.stl |
| .  | .  | 1  | .  | .  | .  | .  | .  | 1  | Y_Carriage_Left_16.stl |
| .  | .  | 1  | .  | .  | .  | .  | .  | 1  | Y_Carriage_Right_16.stl |
| .  | .  | .  | .  | .  | 1  | .  | .  | 1  | Z_Carriage_Center.stl |
| .  | .  | .  | .  | .  | 2  | .  | .  | 2  | Z_Carriage_Side.stl |
| .  | .  | .  | .  | .  | .  | 1  | .  | 1  | Z_Motor_Mount.stl |
| .  | .  | .  | .  | .  | .  | 1  | .  | 1  | Z_Motor_MountGuide_19mm.stl |
| .  | .  | .  | .  | .  | .  | 2  | .  | 2  | Z_RodMountGuide_50mm.stl |
| 3  | 3  |  21  | 3  | .  | 5  | 4  |  15  | 54  | Total 3D printed parts count |
| | | | | | | | | | **CNC routed parts** |
| .  | .  | .  | .  | .  | .  | .  | 1  | 1  | Back_Panel.dxf |
| .  | .  | .  | .  | .  | .  | .  | 1  | 1  | BaseAL.dxf |
| .  | .  | .  | .  | .  | .  | .  | 1  | 1  | Left_Side_Panel.dxf |
| .  | .  | .  | .  | .  | .  | .  | 1  | 1  | Right_Side_Panel.dxf |
| .  | .  | .  | .  | .  | .  | .  | 4  | 4  | Total CNC routed parts count |

<span></span>
[Top](#TOP)

---

## Printhead_E3DV6 assembly

### Vitamins

|Qty|Description|
|---:|:---|
|4| Bolt M2 caphead x  6mm|
|2| Bolt M3 countersunk x 25mm|
|1| Fan 30mm x 10mm|
|1| Hot end E3D V6 direct 1.75mm|
|1| Square radial fan 3010|
|3| Ziptie 2.5mm x 100mm min length|

### 3D Printed parts

| 1 x Fan_Duct.stl | 1 x Hotend_Clamp.stl | 1 x X_Carriage_Groovemount.stl |
|---|---|---|
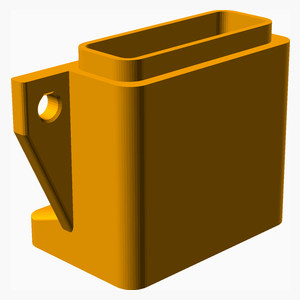
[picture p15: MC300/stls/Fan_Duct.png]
Fan_Duct.stl
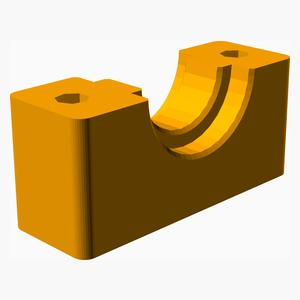
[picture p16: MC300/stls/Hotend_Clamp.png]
Hotend_Clamp.stl
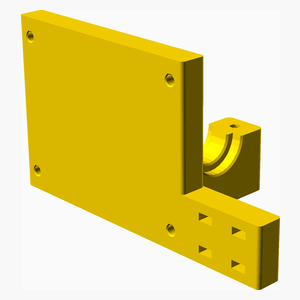
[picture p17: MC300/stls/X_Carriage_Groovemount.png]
X_Carriage_Groovemount.stl
|  |  |  

### Assembly instructions

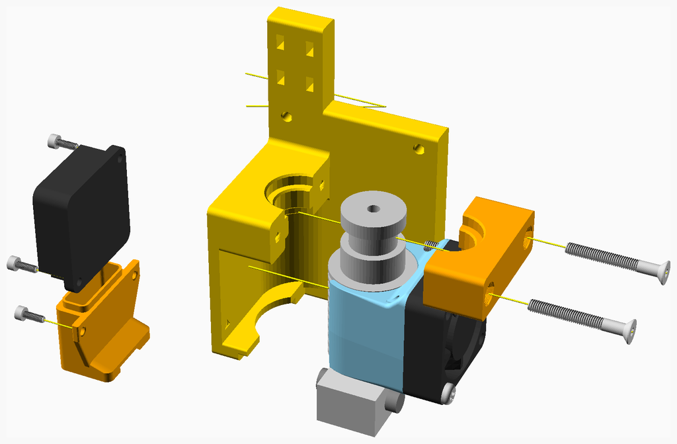
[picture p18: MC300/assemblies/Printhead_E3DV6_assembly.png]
Printhead_E3DV6_assembly


1. Bolt the fan onto the side of the **X_Carriage_Groovemount**, secure the fan wire with a ziptie.
2. Ensure a good fit between the fan and the **Fan_Duct** and bolt the fan duct to the X_Carriage.
3. Assemble the E3D hotend, including fan, thermistor cartridge and heater cartridge.
4. Use the **Hotend_Clamp** to attach the E3D hotend to the X_Carriage.
5. Collect the wires together, wrap them in spiral wrap, and secure them to the X_Carriage using the zipties. Note that the wiring is not shown in this diagram.

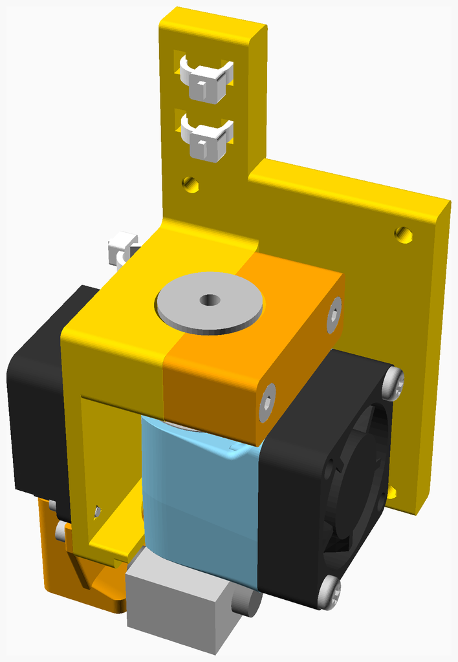
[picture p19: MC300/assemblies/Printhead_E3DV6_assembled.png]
Printhead_E3DV6_assembled


<span></span>
[Top](#TOP)

---

## X_Carriage_Belt_Side assembly

### Vitamins

|Qty|Description|
|---:|:---|
|2| Bolt M3 caphead x 40mm|
|2| Washer  M3|

### 3D Printed parts

| 1 x X_Carriage_Belt_Side_16.stl | 2 x X_Carriage_Belt_Tensioner.stl |
|---|---|
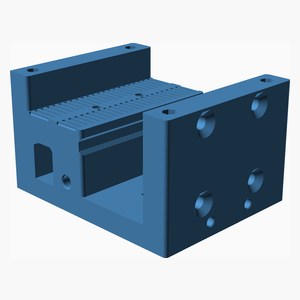
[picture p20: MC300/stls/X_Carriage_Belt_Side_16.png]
X_Carriage_Belt_Side_16.stl
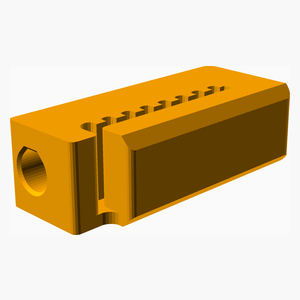
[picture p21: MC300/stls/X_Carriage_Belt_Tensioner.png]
X_Carriage_Belt_Tensioner.stl
|  |  

### Assembly instructions

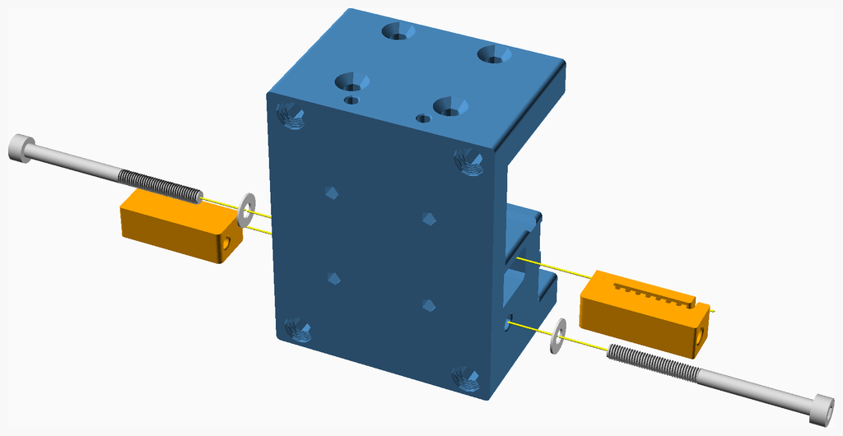
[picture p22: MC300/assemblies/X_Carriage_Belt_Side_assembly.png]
X_Carriage_Belt_Side_assembly


Insert the belts into the **X_Carriage_Belt_Tensioner**s and then bolt the tensioners into the
**X_Carriage_Belt_Side** part as shown. Note the belts are not shown in this diagram.

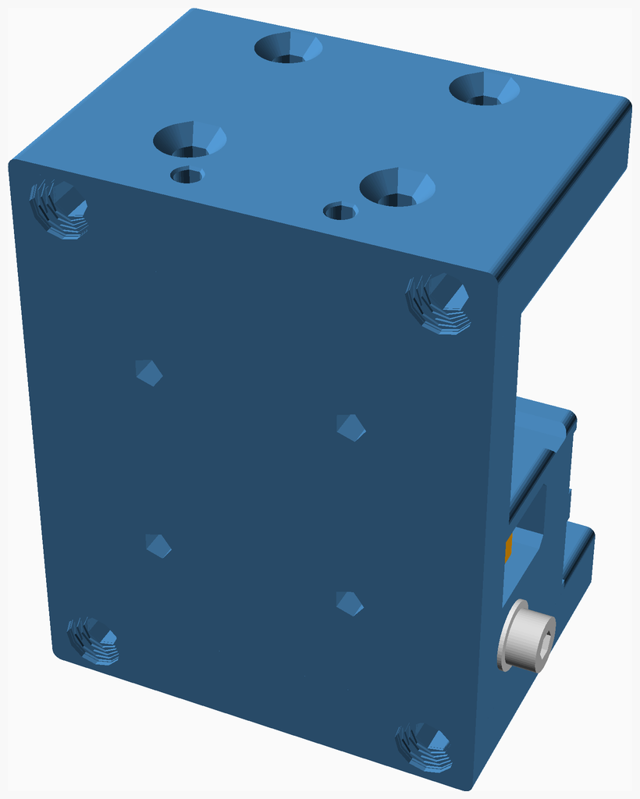
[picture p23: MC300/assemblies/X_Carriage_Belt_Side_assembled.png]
X_Carriage_Belt_Side_assembled


<span></span>
[Top](#TOP)

---

## XY_Motor_Mount_Right assembly

### Vitamins

|Qty|Description|
|---:|:---|
|4| Bolt M3 buttonhead x 12mm|
|4| Bolt M3 countersunk x 25mm|
|3| Bolt M4 buttonhead x 10mm|
|1| Cork damper NEMA 17|
|3| Nut M4 hammer|
|1| Pulley GT2 idler 16 teeth|
|1| Pulley GT2 idler smooth 9.63mm|
|1| Pulley GT2OB 20 teeth|
|1| Stepper motor NEMA17 x 47mm|
|1| Stepper motor cable, 300mm|
|4| Washer  M3|

### 3D Printed parts

| 1 x XY_Motor_Mount_Brace_Right_16.stl | 1 x XY_Motor_Mount_Right_16.stl |
|---|---|
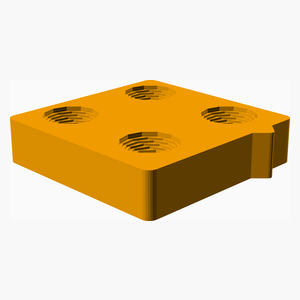
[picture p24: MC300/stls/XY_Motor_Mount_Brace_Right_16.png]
XY_Motor_Mount_Brace_Right_16.stl
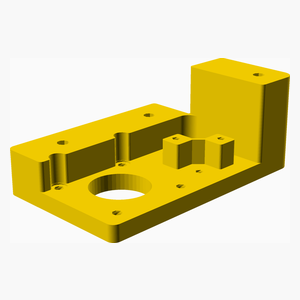
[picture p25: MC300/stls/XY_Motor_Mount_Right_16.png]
XY_Motor_Mount_Right_16.stl
|  |  

### Assembly instructions

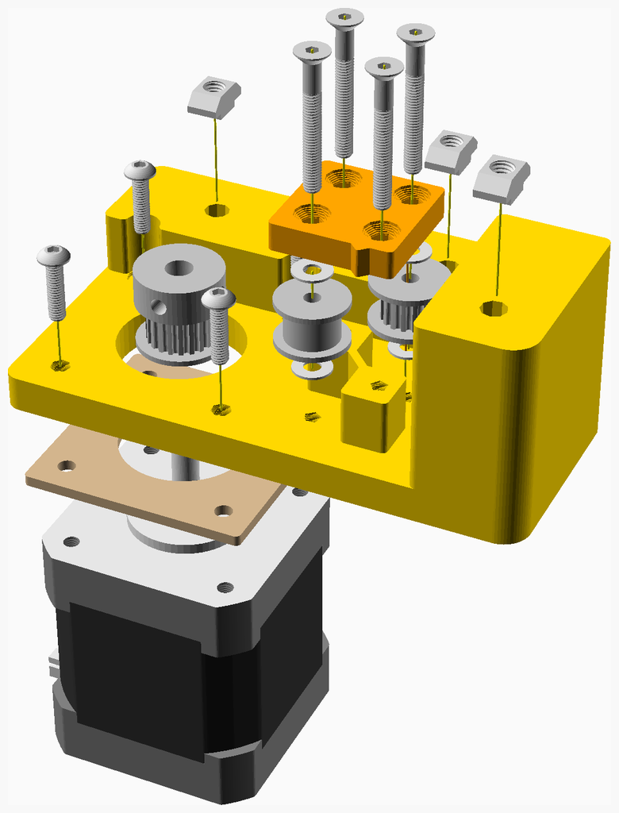
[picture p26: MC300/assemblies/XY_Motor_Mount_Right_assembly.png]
XY_Motor_Mount_Right_assembly


1. Bolt the idler pulleys and the **XY_Motor_Mount_Brace_Right** to the **XY_Motor_Mount_Right**. Note the brace is not
symmetrical - there is an orientation indicator and this should point towards the back of the printer. Tighten the
pulley bolts until the pulleys no longer turn freely, and then loosen the bolts by about 1/4 turn until the pulleys
turn freely again.
2. Bolt the motor and the cork damper to the motor mount. The core damper thermally insulates the motor from the mount
and should not be omitted.
3. Align the drive pulley with the idler pulleys and bolt it to the motor shaft.
4. Add the bolts and t-nuts in preparation for later attachment to the frame.

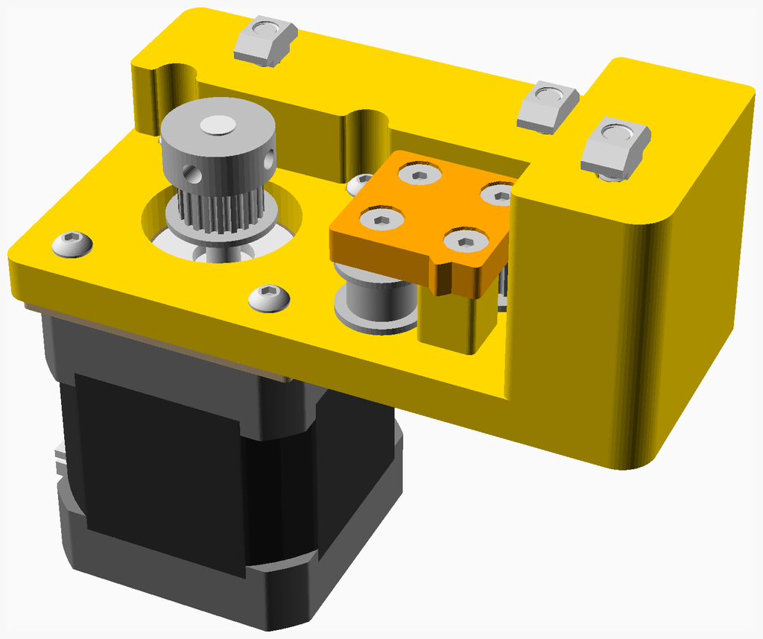
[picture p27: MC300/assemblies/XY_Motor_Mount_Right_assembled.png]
XY_Motor_Mount_Right_assembled


<span></span>
[Top](#TOP)

---

## XY_Motor_Mount_Left assembly

### Vitamins

|Qty|Description|
|---:|:---|
|4| Bolt M3 buttonhead x 12mm|
|4| Bolt M3 countersunk x 25mm|
|3| Bolt M4 buttonhead x 10mm|
|1| Cork damper NEMA 17|
|3| Nut M4 hammer|
|1| Pulley GT2 idler 16 teeth|
|1| Pulley GT2 idler smooth 9.63mm|
|1| Pulley GT2OB 20 teeth|
|1| Stepper motor NEMA17 x 47mm|
|1| Stepper motor cable, 500mm|
|4| Washer  M3|

### 3D Printed parts

| 1 x XY_Motor_Mount_Brace_Left_16.stl | 1 x XY_Motor_Mount_Left_16.stl |
|---|---|
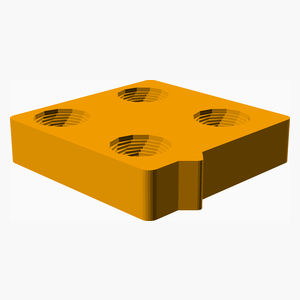
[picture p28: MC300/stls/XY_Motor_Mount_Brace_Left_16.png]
XY_Motor_Mount_Brace_Left_16.stl
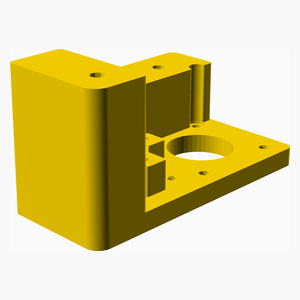
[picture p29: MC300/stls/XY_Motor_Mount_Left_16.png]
XY_Motor_Mount_Left_16.stl
|  |  

### Assembly instructions

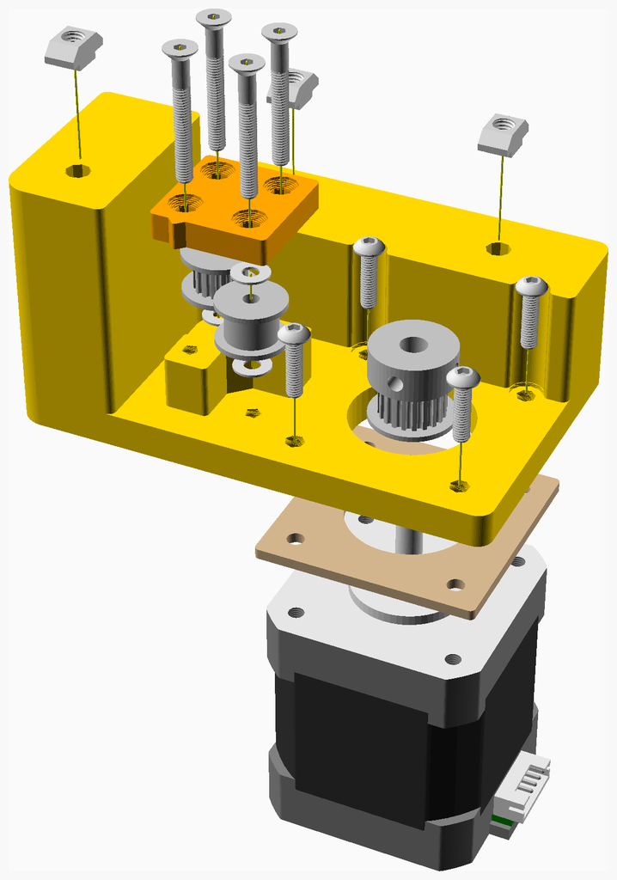
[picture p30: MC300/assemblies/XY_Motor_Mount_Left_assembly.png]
XY_Motor_Mount_Left_assembly


1. Bolt the idler pulleys and the **XY_Motor_Mount_Brace_Left** to the **XY_Motor_Mount_Left**. Note the brace is not
symmetrical - there is an orientation indicator and this should point towards the back of the printer. Tighten the
pulley bolts until the pulleys no longer turn freely, and then loosen the bolts by about 1/4 turn until the pulleys
turn freely again.
2. Bolt the motor and the cork damper to the motor mount. The core damper thermally insulates the motor from the mount
and should not be omitted.
3. Align the drive pulley with the idler pulleys and bolt it to the motor shaft.
4. Add the bolts and t-nuts in preparation for later attachment to the frame.

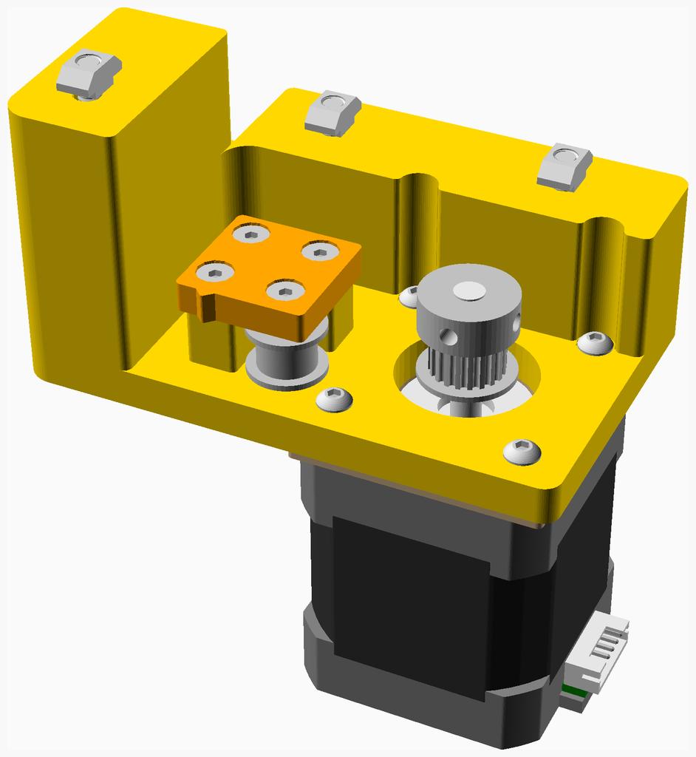
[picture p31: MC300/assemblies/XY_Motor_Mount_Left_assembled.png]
XY_Motor_Mount_Left_assembled


<span></span>
[Top](#TOP)

---

## XY_Idler_Right assembly

### Vitamins

|Qty|Description|
|---:|:---|
|1| Bolt M3 caphead x 30mm|
|4| Bolt M4 buttonhead x 10mm|
|1| Nut M4 hammer|
|2| Pulley GT2 idler 16 teeth|
|6| Washer  M3|
|1| Washer  M4|

### 3D Printed parts

| 1 x XY_Idler_Channel_Nut.stl | 1 x XY_Idler_Right_16.stl |
|---|---|
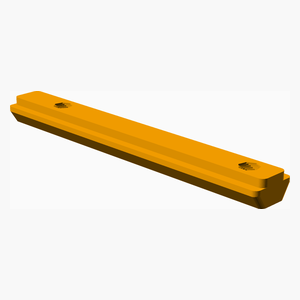
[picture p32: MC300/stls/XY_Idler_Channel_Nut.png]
XY_Idler_Channel_Nut.stl
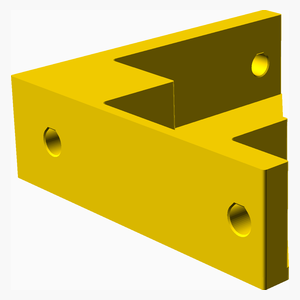
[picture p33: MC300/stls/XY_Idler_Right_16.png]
XY_Idler_Right_16.stl
|  |  

### Assembly instructions

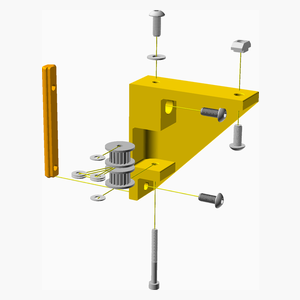
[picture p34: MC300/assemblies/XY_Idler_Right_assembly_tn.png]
XY_Idler_Right_assembly


1. Bolt the pulley stack into the **XY_Idler_Right**. Note that there are 4 washers between the two pulleys and one
washer at the top and the bottom of the pulley stack.
2. Tighten the bolt until the pulleys no longer turn freely, and then loosen the bolt by about 1/4 turn to allow the pulleys
to turn freely again.
3. Add the bolts and t-nuts in preparation for later attachment to the frame.
4. Add the button head bolt and washer.

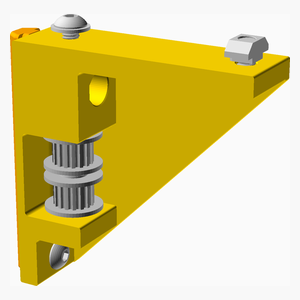
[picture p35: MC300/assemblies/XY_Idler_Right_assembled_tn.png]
XY_Idler_Right_assembled


<span></span>
[Top](#TOP)

---

## XY_Idler_Left assembly

### Vitamins

|Qty|Description|
|---:|:---|
|1| Bolt M3 caphead x 30mm|
|4| Bolt M4 buttonhead x 10mm|
|1| Nut M4 hammer|
|2| Pulley GT2 idler 16 teeth|
|6| Washer  M3|
|1| Washer  M4|

### 3D Printed parts

| 1 x XY_Idler_Channel_Nut.stl | 1 x XY_Idler_Left_16.stl |
|---|---|
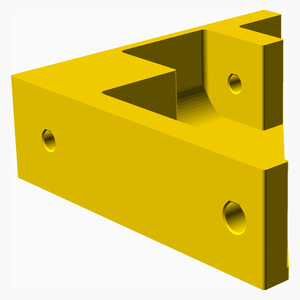
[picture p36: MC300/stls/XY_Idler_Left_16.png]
XY_Idler_Left_16.stl
| XY_Idler_Channel_Nut.stl |  

### Assembly instructions

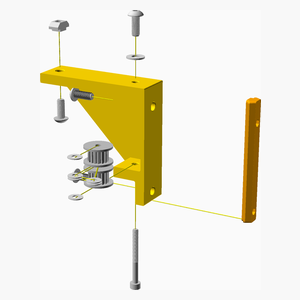
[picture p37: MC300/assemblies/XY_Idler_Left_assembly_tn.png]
XY_Idler_Left_assembly


1. Bolt the pulley stack into the **XY_Idler_Left**. Note that there are 4 washers between the two pulleys and one
washer at the top and the bottom of the pulley stack.
2. Tighten the bolt until the pulleys no longer turn freely, and then loosen the bolt by about 1/4 turn to allow the pulleys
to turn freely again.
3. Add the bolts and t-nuts in preparation for later attachment to the frame.
4. Add the button head bolt and washer.

XY_Idler_Left_assembled

<span></span>
[Top](#TOP)

---

## Y_Carriage_Right assembly

### Vitamins

|Qty|Description|
|---:|:---|
|2| Bolt M3 caphead x 10mm|
|1| Bolt M3 caphead x 16mm|
|1| Bolt M3 caphead x 25mm|
|2| Heatfit insert M3|
|1| Pulley GT2 idler 16 teeth|
|1| Pulley GT2 idler smooth 9.63mm|
|3| Washer  M3|

### 3D Printed parts

| 1 x Y_Carriage_Brace_Right_16.stl | 1 x Y_Carriage_Right_16.stl |
|---|---|
| Y_Carriage_Brace_Right_16.stl | Y_Carriage_Right_16.stl 

### Assembly instructions

Y_Carriage_Right_assembly

1. Insert the threaded inserts into the **Y_Carriage_Right** as shown.
2. Drive a long M3 bolt through the Y carriage from the insert side to self tap the part of the hole after the insert. Once this
hole is tapped, remove the bolt.
3. Bolt the **Y_Carriage_Brace_Right** and the pulleys to the **Y_Carriage_Right** as shown. Note the position of the washers.
4. Tighten the bolts until the pulleys no longer turn freely and then loosen by about 1/4 turn so the pulleys can again turn.

Y_Carriage_Right_assembled

<span></span>
[Top](#TOP)

---

## Right_Side_Upper_Extrusion assembly

### Vitamins

|Qty|Description|
|---:|:---|
|12| Bolt M3 caphead x 10mm|
|4| Bolt M5 buttonhead x 12mm|
|1| Extrusion E2040 x 300mm|
|1| Linear rail MGN12 x 300mm|
|1| Linear rail carriage MGN12H|
|8| Nut M3 hammer|

### Sub-assemblies

| 1 x Y_Carriage_Right_assembly |
|---|
| Y_Carriage_Right_assembled 

### Assembly instructions

Right_Side_Upper_Extrusion_assembly

1. Bolt the MGN linear rail to the extrusion, using the **Rail_Centering_Jig** to align the rail. Do not fully tighten the
bolts at this stage - they will be fully tightened when the rail is racked at a later stage.
2. Bolt the **Y_Carriage_Right_assembly** to the MGN carriage.
3. Screw the bolts into ends of the extrusion in preparation for attachment to the rest of the top face.

Right_Side_Upper_Extrusion_assembled

<span></span>
[Top](#TOP)

---

## Y_Carriage_Left assembly

### Vitamins

|Qty|Description|
|---:|:---|
|2| Bolt M3 caphead x 10mm|
|1| Bolt M3 caphead x 16mm|
|1| Bolt M3 caphead x 25mm|
|2| Heatfit insert M3|
|1| Pulley GT2 idler 16 teeth|
|1| Pulley GT2 idler smooth 9.63mm|
|3| Washer  M3|

### 3D Printed parts

| 1 x Y_Carriage_Brace_Left_16.stl | 1 x Y_Carriage_Left_16.stl |
|---|---|
| Y_Carriage_Brace_Left_16.stl | Y_Carriage_Left_16.stl 

### Assembly instructions

Y_Carriage_Left_assembly

1. Insert the threaded inserts into the **Y_Carriage_Left** as shown.
2. Drive a long M3 bolt through the Y carriage from the insert side to self tap the part of the hole after the insert. Once this
hole is tapped, remove the bolt.
3. Bolt the **Y_Carriage_Brace_Left** and the pulleys to the **Y_Carriage_Left** as shown. Note the position of the washers.
4. Tighten the bolts until the pulleys no longer turn freely and then loosen by about 1/4 turn so the pulleys can again turn.

Y_Carriage_Left_assembled

<span></span>
[Top](#TOP)

---

## Left_Side_Upper_Extrusion assembly

### Vitamins

|Qty|Description|
|---:|:---|
|12| Bolt M3 caphead x 10mm|
|4| Bolt M5 buttonhead x 12mm|
|1| Extrusion E2040 x 300mm|
|1| Linear rail MGN12 x 300mm|
|1| Linear rail carriage MGN12H|
|8| Nut M3 hammer|

### Sub-assemblies

| 1 x Y_Carriage_Left_assembly |
|---|
| Y_Carriage_Left_assembled 

### Assembly instructions

Left_Side_Upper_Extrusion_assembly

1. Bolt the MGN linear rail to the extrusion, using the **Rail_Centering_Jig** to align the rail. Fully tighten the
bolts - the left rail is the fixed rail and the right rail will be aligned to it.
bolts at this stage - they will be fully tightened when the rail is racked at a later stage.
2. Bolt the **Y_Carriage_Left_assembly** to the MGN carriage.
3. Screw the bolts into ends of the extrusion in preparation for attachment to the rest of the top face.

Left_Side_Upper_Extrusion_assembled

<span></span>
[Top](#TOP)

---

## Face_Top_Stage_1 assembly

### Vitamins

|Qty|Description|
|---:|:---|
|4| Bolt M2 caphead x  8mm|
|2| Bolt M3 buttonhead x 10mm|
|2| Bolt M4 buttonhead x 10mm|
|20| Bolt M4 countersunk x 10mm|
|4| Bolt M5 buttonhead x 10mm|
|2| Bolt M5 buttonhead x 12mm|
|1| Extrusion E2020 x 300mm|
|1| Extrusion E2040 x 300mm|
|2| Nut M3 hammer|
|2| Nut M4 hammer|
|28| Nut M4 sliding T|
|1| Raspberry Pi camera V2|

### 3D Printed parts

| 1 x Camera_Mount.stl | 4 x Top_Corner_Piece.stl | 1 x Wiring_Guide_Socket.stl |
|---|---|---|
| Camera_Mount.stl | Top_Corner_Piece.stl | Wiring_Guide_Socket.stl 

### Sub-assemblies

| 1 x Left_Side_Upper_Extrusion_assembly | 1 x Right_Side_Upper_Extrusion_assembly | 1 x XY_Idler_Left_assembly |
|---|---|---|
| Left_Side_Upper_Extrusion_assembled | Right_Side_Upper_Extrusion_assembled | XY_Idler_Left_assembled 

| 1 x XY_Idler_Right_assembly | 1 x XY_Motor_Mount_Left_assembly | 1 x XY_Motor_Mount_Right_assembly |
|---|---|---|
| XY_Idler_Right_assembled | XY_Motor_Mount_Left_assembled | XY_Motor_Mount_Right_assembled 

### Assembly instructions

Face_Top_Stage_1_assembly

1. Bolt the two motor mounts, the **Wiring_Guide**, and optionally the **Camera_Mount** to the rear extrusion.
2. Bolt the two idlers to the front extrusion.
3. Screw the bolts into the ends of the front and rear extrusions.
4. Insert the t-nuts for the **Handle** into the extrusions.
5. Insert the t-nuts for the **Top_Corner_Piece**s into the extrusions.
6. Bolt the front and rear extrusions to the side extrusions, leaving the bolts slightly loose.
7. Bolt the **Top_Corner_Piece**s to the extrusions leaving the bolts slightly loose.
8. Turn the top face upside down and place on a flat surface. Ensure it is square and tighten the hidden bolts.
9. Turn the top face the right way up and tighten the bolts on the **Top_Corner_Piece**s.

Face_Top_Stage_1_assembled

<span></span>
[Top](#TOP)

---

## Face_Top_Stage_2 assembly

### Vitamins

|Qty|Description|
|---:|:---|
|4| Bolt M3 caphead x 10mm|
|1| Linear rail MGN12 x 250mm|
|1| Linear rail carriage MGN12H|

### Sub-assemblies

| 1 x Face_Top_Stage_1_assembly |
|---|
| Face_Top_Stage_1_assembled 

### Assembly instructions

Face_Top_Stage_2_assembly

1. Bolt the MGN rail to the Y_Carriages as shown. Ensure the MGN rail is square to the frame.
2. Turn the top face upside down and place on a flat surface. Rack the right side linear rail - move the X-rail
to one extreme of the frame and tighten the bolts on that end of the Y-rail. Then move the X-rail to the other
extreme and tighten the bolts on that end of the Y-rail. Finally tighten the remaining bolts on the Y-rail.
3. Ensure the X-rail moves freely, if it doesn't loosen the bolts you have just tightened and repeat step 2.

Face_Top_Stage_2_assembled

<span></span>
[Top](#TOP)

---

## Face_Top assembly

### Vitamins

|Qty|Description|
|---:|:---|
|1| Belt GT2 x 6mm x 1260mm|
|1| Belt GT2 x 6mm x 1270mm|
|2| Bolt M3 countersunk x 10mm|
|4| Bolt M3 countersunk x 12mm|
|8| Bolt M4 buttonhead x 12mm|
|8| Nut M4 sliding T|

### 3D Printed parts

| 2 x Handle.stl | 1 x X_Carriage_Belt_Clamp.stl |
|---|---|
| Handle.stl | X_Carriage_Belt_Clamp.stl 

### Sub-assemblies

| 1 x Face_Top_Stage_2_assembly | 1 x X_Carriage_Belt_Side_assembly |
|---|---|
| Face_Top_Stage_2_assembled | X_Carriage_Belt_Side_assembled 

### Assembly instructions

Face_Top_assembly

1. Bolt the **X_Carriage_Belt_Side_assembly** to the MGN carriage.
2. Thread the belts as shown and attach them to the **X_Carriage_Belt_Side_assembly**
using the **X_Carriage_Belt_Clamp**.
3. Leave the belts fairly loose - tensioning of the belts is done after the frame is assembled.
4. Bolt the handles to the previously inserted t-nuts.

Face_Top_assembled

<span></span>
[Top](#TOP)

---

## Extruder_Bracket assembly

### Vitamins

|Qty|Description|
|---:|:---|
|2| Bolt M3 buttonhead x 16mm|
|2| Bolt M3 countersunk x  8mm|
|4| Bolt M4 buttonhead x  8mm|
|1| Cork damper NEMA 17|
|1| Filament sensor|
|1| MK10 Dual Pulley Extruder|
|4| Nut M4 hammer|
|2| Pillar hex nylon F/F M3x14|
|1| Stepper motor NEMA17 x 47mm|
|1| Stepper motor cable, 200mm|

### 3D Printed parts

| 1 x Extruder_Bracket.stl |
|---|
| Extruder_Bracket.stl 

### Assembly instructions

Extruder_Bracket_assembly

1. Bolt the stepper motor and cork damper through the **Extruder_Bracket** to the extruder as shown. The cork damper
thermally isolates the motor from the **Extruder_Bracket** and should not be omitted.
2. Align the hobb gear on the stepper motor shaft with the the hobb gear in the extruder and tighten the grub screws.
3. Bolt the filament sensor to the hex pillars and bolt them to the **Extruder_Bracket**.
4. Add the bolts and t-nuts in preparation for later attachment to the frame.

Extruder_Bracket_assembled

<span></span>
[Top](#TOP)

---

## Right_Side assembly

### Vitamins

|Qty|Description|
|---:|:---|
|5| Bolt M4 buttonhead x  8mm|
|6| Bolt M5 buttonhead x 12mm|
|1| Extrusion E2020 x 300mm|
|2| Extrusion E2020 x 400mm|
|1| Extrusion E2040 x 300mm|
|4| Nut M4 hammer|

### 3D Printed parts

| 1 x Right_Side_Panel.stl | 1 x Right_Side_Panel_Bracket.stl |
|---|---|
| Right_Side_Panel.stl | Right_Side_Panel_Bracket.stl 

### Sub-assemblies

| 1 x Extruder_Bracket_assembly |
|---|
| Extruder_Bracket_assembled 

### Assembly instructions

Right_Side_assembly

1. On a flat surface, bolt the upper and lower extrusions into the left and right uprights as shown.
2. Bolt the **IEC_Housing_assembly** to the lower extrusion and upright.
3. Bolt the **Extruder_Bracket_assembly** to the upper extrusion and upright.

Right_Side_assembled

<span></span>
[Top](#TOP)

---

## Display_Cover_TFT35_E3 assembly

### Vitamins

|Qty|Description|
|---:|:---|
|1| BigTreeTech TFT35 E3 v3.0|
|4| Bolt M3 caphead x  6mm|

### 3D Printed parts

| 1 x Display_Housing_TFT35_E3.stl |
|---|
| Display_Housing_TFT35_E3.stl 

### Assembly instructions

Display_Cover_TFT35_E3_assembly

1. Bolt the TFT35 E3 display to the **Display_Housing_TFT35_E3**.
2. Attach the knob to the display.

Display_Cover_TFT35_E3_assembled

<span></span>
[Top](#TOP)

---

## IEC_Housing assembly

### Vitamins

|Qty|Description|
|---:|:---|
|5| Bolt M4 buttonhead x  8mm|
|2| Bolt M4 buttonhead x 12mm|
|1| IEC320 C14 switched fused inlet module|
|5| Nut M4 hammer|

### 3D Printed parts

| 1 x IEC_Housing.stl | 1 x IEC_Housing_Mount.stl |
|---|---|
| IEC_Housing.stl | IEC_Housing_Mount.stl 

### Assembly instructions

IEC_Housing_assembly

1. Attach the power cables to the IEC connector.
2. Thread the power cables through the hole in the **IEC_Housing** and bolt the **IEC_Housing_Mount** to the **IEC_housing**.
3. Add the bolts and t-nuts in preparation for attachment to the frame.

IEC_Housing_assembled

<span></span>
[Top](#TOP)

---

## Base_Plate_Stage_1 assembly

### Vitamins

|Qty|Description|
|---:|:---|
|1| Aluminium sheet 340mm x 340mm x 3mm|
|1| BigTreeTech Relay Module v1.2|
|1| BigTreeTech SKR v1.4 Turbo|
|16| Bolt M3 buttonhead x 10mm|
|16| Bolt M3 caphead x  6mm|
|8| Bolt M4 buttonhead x  8mm|
|10| Bolt M4 buttonhead x 10mm|
|14| Bolt M5 buttonhead x 12mm|
|1| Extrusion E2020 x 300mm|
|1| Extrusion E2040 x 300mm|
|1| Extrusion E2080 x 300mm|
|1| Micro SD card|
|16| Nut M4 hammer|
|1| PSU NIUGUY CB-500W-24V|
|12| Pillar hex nylon F/F M3x10|
|4| Pillar hex nylon F/F M3x20|
|1| Raspberry Pi 3A+|
|1| XL4015 buck converter|

### 3D Printed parts

| 4 x Foot_LShaped_12mm.stl |
|---|
| Foot_LShaped_12mm.stl 

### CNC Routed parts

| 1 x BaseAL.dxf |
|---|
| BaseAL.dxf 

### Sub-assemblies

| 1 x IEC_Housing_assembly |
|---|
| IEC_Housing_assembled 

### Assembly instructions

Base_Plate_Stage_1_assembly

If you have access to a CNC, you can machine the base plate using **BaseAL.dxf**, if not you can use the **Panel_Jig**
as a template to drill the holes in the base plate.

1. Insert the bolts into the ends of the E2040 and E2080 extrusions in preparation for connection to the frame uprights.
2. Bolt the extrusions and the L-shaped feet to the baseplate as shown.
3. Bolt the PSU and the pcbs to the baseplate, using standoffs as appropriate.

Base_Plate_Stage_1_assembled

<span></span>
[Top](#TOP)

---

## Base_Plate assembly

### Vitamins

|Qty|Description|
|---:|:---|
|4| Bolt M3 buttonhead x 12mm|
|4| Bolt M3 caphead x 25mm|
|4| Bolt M4 buttonhead x 10mm|
|4| Nut M3 hammer|
|4| Nut M4 hammer|

### 3D Printed parts

| 1 x Display_Housing_Bracket_TFT35_E3.stl | 1 x Front_Cover_300.stl | 1 x Front_Display_Wiring_Cover_300.stl |
|---|---|---|
| Display_Housing_Bracket_TFT35_E3.stl | Front_Cover_300.stl | Front_Display_Wiring_Cover_300.stl 

### Sub-assemblies

| 1 x Base_Plate_Stage_1_assembly | 1 x Display_Cover_TFT35_E3_assembly |
|---|---|
| Base_Plate_Stage_1_assembled | Display_Cover_TFT35_E3_assembled 

### Assembly instructions

Base_Plate_assembly

1. Bolt the **Display_Housing_Bracket_TFT35_E3** to the 2080 extrusion.
2. Thread the display wiring through the hole in the **Display_Housing_Bracket_TFT35_E3** and connect it to the TFT display.
3. Bolt the **Display_Cover_TFT35_E3_assembly** to the **Display_Housing_Bracket_TFT35_E3**.
4. Bolt the **Front_Cover** to the top of the 2080 extrusion.
5. Bolt the **Front_Display_Wiring_Cover** to the top of the 2080 extrusion, covering the wiring.
6. Route the wiring to the back of the base, ready for later connection to the mainboard.

Base_Plate_assembled

<span></span>
[Top](#TOP)

---

## Heated_Bed assembly

### Vitamins

|Qty|Description|
|---:|:---|
|3| Bolt M3 caphead x 20mm|
|1| Heated Bed 214mm x 214mm|
|3| Nut M3 hammer|
|12| O-ring nitrile 4mm x 2mm|
|12| Washer  M3|
|3| Washer penny  M4|

### Assembly instructions

Heated_Bed_assembly

1. Attach the print surface to the heated bed.
2. Insert a bolt into each of the bolt holes in the heated bed and add a stack of O-rings, washers and a hammer nut as shown.
3

Heated_Bed_assembled

<span></span>
[Top](#TOP)

---

## 2 x Z_Carriage_Side assembly

### Vitamins

|Qty|Description|
|---:|:---|
|2| Bolt M4 buttonhead x 10mm|
|4| Bolt M5 buttonhead x 16mm|
|4| Bolt M5 countersunk x 12mm|
|2| Nut M4 sliding T|
|2| SCS12LUU bearing block|

### 3D Printed parts

| 2 x Z_Carriage_Side.stl |
|---|
| Z_Carriage_Side.stl 

### Assembly instructions

Z_Carriage_Side_assembly

1. Bolt the SCS bearing block to the **Z_Carriage**.
2. Add the bolts and t-nuts in preparation for connection to the printbed.

Z_Carriage_Side_assembled

<span></span>
[Top](#TOP)

---

## Z_Carriage_Center assembly

### Vitamins

|Qty|Description|
|---:|:---|
|4| Bolt M3 caphead x 10mm|
|4| Bolt M4 buttonhead x 10mm|
|1| Leadscrew nut 8 x 2|
|4| Nut M4 sliding T|

### 3D Printed parts

| 1 x Z_Carriage_Center.stl |
|---|
| Z_Carriage_Center.stl 

### Assembly instructions

Z_Carriage_Center_assembly

1. Bolt the leadscrew to the **Z_Carriage_Center**.
2. Add the bolts and t-nuts in preparation for later attachment to the printbed frame.

Z_Carriage_Center_assembled

<span></span>
[Top](#TOP)

---

## Printbed_Frame assembly

### Vitamins

|Qty|Description|
|---:|:---|
|2| Bolt M3 countersunk x 10mm|
|8| Bolt M5 buttonhead x 12mm|
|2| Extrusion E2020 x 265mm|
|2| Extrusion E2040 x 188mm|
|2| Nut M3 hammer|

### 3D Printed parts

| 1 x Printbed_Strain_Relief.stl |
|---|
| Printbed_Strain_Relief.stl 

### Sub-assemblies

| 1 x Z_Carriage_Center_assembly |
|---|
| Z_Carriage_Center_assembled 

### Assembly instructions

Printbed_Frame_assembly

1. Slide the **Z_Carriage_Center_assembly** to the approximate center of the first 2040 extrusion and loosely tighten the bolts.
The bolts will be fully tightened when the Z_Carriage is aligned.
2. Bolt the **Printbed_Strain_Relief** to the second extrusion.
3. Slide the 2040 extrusion into the 2020 extrusions and loosely tighten the bolts. The bolts will be fully tightened after
the Z carriages are added.

Printbed_Frame_assembled

<span></span>
[Top](#TOP)

---

## Printbed_Frame_with_Z_Carriages assembly

### Sub-assemblies

| 1 x Printbed_Frame_assembly | 2 x Z_Carriage_Side_assembly |
|---|---|
| Printbed_Frame_assembled | Z_Carriage_Side_assembled 

### Assembly instructions

Printbed_Frame_with_Z_Carriages_assembly

1. Lay the frame on a flat surface and  slide the Z carriages onto the frame as shown.
2. Ensure the Z carriages are square and aligned with the end of the frame and then tighten the bolts on Z_carriages.
3. Ensure the 2040 extrusion is pressed firmly against the Z_Carriages and tighten the hidden bolts in the frame.

Printbed_Frame_with_Z_Carriages_assembled

<span></span>
[Top](#TOP)

---

## Printbed assembly

### Vitamins

|Qty|Description|
|---:|:---|
|2| Bolt M3 buttonhead x  8mm|
|1| Cork underlay 214mm x 214mm|

### 3D Printed parts

| 1 x Printbed_Strain_Relief_Clamp.stl |
|---|
| Printbed_Strain_Relief_Clamp.stl 

### Sub-assemblies

| 1 x Heated_Bed_assembly | 1 x Printbed_Frame_with_Z_Carriages_assembly |
|---|---|
| Heated_Bed_assembled | Printbed_Frame_with_Z_Carriages_assembled 

### Assembly instructions

Printbed_assembly

1. Attach the heated bed to the frame using the stacks of washers and O-rings as shown.
2. Spiral wrap the wires from the heated bed.
3. Use the **Printbed_Strain_Relief_Clamp** to clamp the wires to the frame.

Printbed_assembled

<span></span>
[Top](#TOP)

---

## Left_Side assembly

### Vitamins

|Qty|Description|
|---:|:---|
|2| Bolt M4 buttonhead x 10mm|
|2| Bolt M4 buttonhead x 12mm|
|8| Bolt M4 countersunk x 10mm|
|8| Bolt M5 buttonhead x 12mm|
|2| Extrusion E2020 x 400mm|
|2| Extrusion E2040 x 300mm|
|12| Nut M4 sliding T|
|4| SK12 shaft support bracket|

### 3D Printed parts

| 1 x Z_Motor_Mount.stl | 1 x Z_Motor_MountGuide_19mm.stl | 2 x Z_RodMountGuide_50mm.stl |
|---|---|---|
| Z_Motor_Mount.stl | Z_Motor_MountGuide_19mm.stl | Z_RodMountGuide_50mm.stl 

### Assembly instructions

Left_Side_assembly

1. Attach the SK brackets to the upper extrusion, use the **Z_RodMountGuide** to align the left bracket.
2. Tighten the bolts for the left bracket. Leave the bolts to the right bracket loosely tightened for now.
3. Attach the SK brackets and the **Z_Motor_Mount** to the lower extrusion, use the **Z_RodMountGuide** to
align the left bracket and the **Z_Motor_MountGuide** to align the motor mount. The motor itself will be added at a later
stage of the assembly.
4. Tighten the bolts for the left bracket and the **Z_Motor_Mount**. Leave the bolts to the right bracket loosely tightened for now.
5. On a flat surface, bolt the upper and lower extrusions into the left and right uprights as shown. Tighten the bolts
continuously ensuring the frame is square.

Left_Side_assembled

<span></span>
[Top](#TOP)

---

## Left_Side_with_Printbed assembly

### Vitamins

|Qty|Description|
|---:|:---|
|4| Bolt M3 buttonhead x 12mm|
|1| Cork damper NEMA 17|
|2| Linear rod 12mm x 300mm|
|1| Stepper motor NEMA17 x 40mm, 280mm integrated leadscrew|
|1| Stepper motor cable, 750mm|

### Sub-assemblies

| 1 x Left_Side_assembly | 1 x Printbed_assembly |
|---|---|
| Left_Side_assembled | Printbed_assembled 

### Assembly instructions

Left_Side_with_Printbed_assembly

1. Face the left face on a flat surface.
2. Attach the print bed to the left face by sliding the linear rods through the Z_Carriages.
3. Tighten the grub screws on the rod brackets, but don't yet tighten the bolts holding the brackets to the frame.
4. Slide the print bed to the top of the rods, and tighten the bolts in the top right rod bracket.
(you will have tightened the bolts on the top left bracket in a previous step).
5. Slide the print bed to the bottom of the rods and tighten the bolts on the bottom right rod bracket
(you will have tightened the bolts on the bottom left bracket in a previous step).
6. Thread the motor's lead screw through the lead nut on the **Z_Carriage_Center** and loosely bolt the motor to
the **Z_Motor_Mount**.
7. Ensure the **Z_Carriage_Center** is aligned with the lead screw and tighten the bolts on the **Z_Carriage_Center**
and the **Z_Motor_Mount**. The bolt holes on the **Z_Motor_Mount** are oval to allow some adjustment.
8. Route the motor wire through the lower extrusion channel and use the **E20_ChannelCover_50mm**s to hold it in place.

Left_Side_with_Printbed_assembled

<span></span>
[Top](#TOP)

---

## Stage_1 assembly

### Sub-assemblies

| 1 x Base_Plate_assembly | 1 x Left_Side_with_Printbed_assembly |
|---|---|
| Base_Plate_assembled | Left_Side_with_Printbed_assembled 

### Assembly instructions

Stage_1_assembly

1. Slide the left face into the base plate assembly.
2. Ensuring the frame remains square, tighten the hidden bolts and the bolts under the baseplate.

Stage_1_assembled

<span></span>
[Top](#TOP)

---

## Stage_2 assembly

### Sub-assemblies

| 1 x Right_Side_assembly | 1 x Stage_1_assembly |
|---|---|
| Right_Side_assembled | Stage_1_assembled 

### Assembly instructions

Stage_2_assembly

1. Slide the right face into the base plate assembly.
2. Ensuring the frame remains square, tighten the hidden bolts and the bolts under the baseplate.
3. Route the serial cable for the display in the top channel of the right side lower extrusion and route
the ribbon cable along the bottom of the extrusion and cover with the **E20_RibbonCover_50mm**s to keep
the cables in place.

Stage_2_assembled

<span></span>
[Top](#TOP)

---

## Stage_3 assembly

### Vitamins

|Qty|Description|
|---:|:---|
|14| Bolt M4 countersunk x  8mm|
|14| Nut M4 hammer|
|1| Sheet polycarbonate 340mm x 400mm x 3mm|

### CNC Routed parts

| 1 x Back_Panel.dxf |
|---|
| Back_Panel.dxf 

### Sub-assemblies

| 1 x Face_Top_assembly | 1 x Stage_2_assembly |
|---|---|
| Face_Top_assembled | Stage_2_assembled 

### Assembly instructions

Stage_3_assembly

1. Slide the **Face_Top** assembly into the rest of the frame and tighten the hidden bolts.
2. Check that the print head slides freely on the Y-axis. If it doesn't, then re-rack the Y-axis,
see [Face_Top_Stage_2 assembly](#Face_Top_Stage_2_assembly).
3. Attach the back panel to the rest of the assembly.
4. Tighten the bolts on the back panel.

Stage_3_assembled

<span></span>
[Top](#TOP)

---

## Stage_4 assembly

### Vitamins

|Qty|Description|
|---:|:---|
|2| Bolt M3 buttonhead x  8mm|
|4| Bolt M3 countersunk x 40mm|
|1| PTFE Bowden tube, 500 mm|

### 3D Printed parts

| 1 x Wiring_Guide.stl | 1 x Wiring_Guide_Clamp.stl |
|---|---|
| Wiring_Guide.stl | Wiring_Guide_Clamp.stl 

### Sub-assemblies

| 1 x Printhead_E3DV6_assembly | 1 x Stage_3_assembly |
|---|---|
| Printhead_E3DV6_assembled | Stage_3_assembled 

### Assembly instructions

Stage_4_assembly

1. Bolt the **Printhead_E3DV6_assembly** to the MGN carriage.
2. Route the wiring from the print head to the mainboard and secure it with the **Wiring_Guide_Clamp**.
3. Adjust the belt tension.
4. Connect the Bowden tube between the extruder and the printhead.

Stage_4_assembled

<span></span>
[Top](#TOP)

---

## main assembly

### Vitamins

|Qty|Description|
|---:|:---|
|25| Bolt M4 buttonhead x  8mm|
|2| Bolt M4 buttonhead x 12mm|
|27| Nut M4 hammer|
|1| Sheet polycarbonate 250mm x 400mm x 3mm|
|1| Sheet polycarbonate 340mm x 400mm x 3mm|

### 3D Printed parts

| 1 x Spool_Holder.stl | 1 x Spool_Holder_36.stl | 1 x Spool_Holder_Bracket.stl |
|---|---|---|
| Spool_Holder.stl | Spool_Holder_36.stl | Spool_Holder_Bracket.stl 

### CNC Routed parts

| 1 x Left_Side_Panel.dxf | 1 x Right_Side_Panel.dxf |
|---|---|
| Left_Side_Panel.dxf | Right_Side_Panel.dxf 

### Sub-assemblies

| 1 x Stage_4_assembly |
|---|
| Stage_4_assembled 

### Assembly instructions

main_assembly

1. Bolt the polycarbonate sheet to the left face.
2. Attach the spoolholder and filament spool to the right face.
3. You are now ready to level the bed and calibrate the printer.

main_assembled

<span></span>
[Top](#TOP)

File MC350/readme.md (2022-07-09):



# MaybeCube Assembly Instructions

These are the assembly instructions for the MaybeCube. These instructions are not fully comprehensive, that is they do
not show every small detail of the construction and in particular they do not show the wiring. However there is
sufficient detail that someone with a good understanding of 3D printers can build the MaybeCube.

Main Assembly

## Read this before you order parts

2020, 2040 etc aluminium comes in variants with differing sized center holes - some are suitable for tapping for an
an M5 bolt and some are suitable for tapping for an M6 bolt. It doesn't really matter which you use, but ensure you
buy the bolts that correspond to your extrusion size. These build instructions assume M5 bolts, if your extrusion
requires M6 bolts then the 10mm and 12mm buttonhead M5 bolts should be replaced with M6 bolts.

The motor for the Z-axis has an integrated lead screw: in the *Parts List* the length specified is the length that
protrudes from the motor. Some suppliers specify the total length of the lead screw, that is including the part that
is inside the motor, so check how your supplier specifies the part before ordering. Another option is to order a lead
screw that is too long and cut to size, not however that lead screws are made from hardened steel and cannot be cut
with a hacksaw - an angle grinder is required to cut them.

This is a full build, some parts can be omitted to save cost, in particular:

* the Raspberry Pi camera (and corresponding 8mm M2 caphead bolts)
* the Raspberry Pi (if you don't want to run Octoprint or Klipper) and corresponding buck converter
* the Big Tree Tech relay module, if you don't want auto shut off
* the Big Tree Tech TFT display, if you are running Octoprint or Klipper
* I've specified a Big Tree Tech mainboard and display, you of course can use any mainboard and display you like
* the filament sensor
* the polycarbonate side and back panels, if you don't want to enclose your print volume for (say) printing ABS. Note
that these also add rigidity to the printer.

I've specified buttonhead bolts for the side and back panels. For a neater look you could countersink the holes and
use countersunk bolts.

## Printing the parts

A number of parts are in proximity with heat sources, namely the hotend, the heated bed and the motors. Ideally these
should be printed in ABS, but I have used PETG successfully. These parts are insulated from direct contact with the heat
sources, by cork underlay (for the heated bed) and by cork dampers (for the motors). These insulators should not be
omitted from the build.

<span></span>

---

## Table of Contents

1. [Parts list](#Parts_list)
1. [Printhead_E3DV6 assembly](#Printhead_E3DV6_assembly)
1. [X_Carriage_Belt_Side assembly](#X_Carriage_Belt_Side_assembly)
1. [XY_Motor_Mount_Right assembly](#XY_Motor_Mount_Right_assembly)
1. [XY_Motor_Mount_Left assembly](#XY_Motor_Mount_Left_assembly)
1. [XY_Idler_Right assembly](#XY_Idler_Right_assembly)
1. [XY_Idler_Left assembly](#XY_Idler_Left_assembly)
1. [Y_Carriage_Right assembly](#Y_Carriage_Right_assembly)
1. [Right_Side_Upper_Extrusion assembly](#Right_Side_Upper_Extrusion_assembly)
1. [Y_Carriage_Left assembly](#Y_Carriage_Left_assembly)
1. [Left_Side_Upper_Extrusion assembly](#Left_Side_Upper_Extrusion_assembly)
1. [Face_Top_Stage_1 assembly](#Face_Top_Stage_1_assembly)
1. [Face_Top_Stage_2 assembly](#Face_Top_Stage_2_assembly)
1. [Face_Top assembly](#Face_Top_assembly)
1. [Extruder_Bracket assembly](#Extruder_Bracket_assembly)
1. [Right_Side assembly](#Right_Side_assembly)
1. [Display_Cover_TFT35_E3 assembly](#Display_Cover_TFT35_E3_assembly)
1. [IEC_Housing assembly](#IEC_Housing_assembly)
1. [Base_Plate_Stage_1 assembly](#Base_Plate_Stage_1_assembly)
1. [Base_Plate assembly](#Base_Plate_assembly)
1. [Z_Carriage_Side assembly](#Z_Carriage_Side_assembly)
1. [Z_Carriage_Center assembly](#Z_Carriage_Center_assembly)
1. [Printbed_Frame assembly](#Printbed_Frame_assembly)
1. [Printbed_Frame_with_Z_Carriages assembly](#Printbed_Frame_with_Z_Carriages_assembly)
1. [Printbed assembly](#Printbed_assembly)
1. [Left_Side assembly](#Left_Side_assembly)
1. [Left_Side_with_Printbed assembly](#Left_Side_with_Printbed_assembly)
1. [Stage_1 assembly](#Stage_1_assembly)
1. [Stage_2 assembly](#Stage_2_assembly)
1. [Stage_3 assembly](#Stage_3_assembly)
1. [Stage_4 assembly](#Stage_4_assembly)
1. [Main assembly](#main_assembly)

<span></span>
[Top](#TOP)

---

## Parts list

| <span style="writing-mode: vertical-rl; text-orientation: mixed;">Printhead E3DV6</span> | <span style="writing-mode: vertical-rl; text-orientation: mixed;">X Carriage Belt Side</span> | <span style="writing-mode: vertical-rl; text-orientation: mixed;">Face Top</span> | <span style="writing-mode: vertical-rl; text-orientation: mixed;">Right Side</span> | <span style="writing-mode: vertical-rl; text-orientation: mixed;">Printbed</span> | <span style="writing-mode: vertical-rl; text-orientation: mixed;">Left Side</span> | <span style="writing-mode: vertical-rl; text-orientation: mixed;">Main</span> | <span style="writing-mode: vertical-rl; text-orientation: mixed;">TOTALS</span> |  |
|-----:|-----:|-----:|-----:|-----:|-----:|-----:|---:|:---|
| | | | | | | | | **Vitamins** |
| .  | .  | .  | .  | .  | .  | 1  | 1  |  Aluminium sheet 390mm x 390mm x 3mm |
| .  | .  |  24  | .  | .  | .  | .  | 24  |  Ball bearing F623-2RS 3mm x 10mm x 4mm |
| .  | .  | 1  | .  | .  | .  | .  | 1  |  Belt GT2 x 6mm x 1476mm |
| .  | .  | 1  | .  | .  | .  | .  | 1  |  Belt GT2 x 6mm x 1500mm |
| .  | .  | .  | .  | .  | .  | 1  | 1  |  BigTreeTech Relay Module v1.2 |
| .  | .  | .  | .  | .  | .  | 1  | 1  |  BigTreeTech SKR v1.4 Turbo |
| .  | .  | .  | .  | .  | .  | 1  | 1  |  BigTreeTech TFT35 E3 v3.0 |
| 4  | .  | .  | .  | .  | .  | .  | 4  |  Bolt M2 caphead x  6mm |
| .  | .  | 4  | .  | .  | .  | .  | 4  |  Bolt M2 caphead x  8mm |
| .  | .  |  14  | 2  | 2  | .  |  20  | 38  |  Bolt M3 buttonhead x 10mm |
| .  | .  | .  | .  | .  | .  |  18  | 18  |  Bolt M3 caphead x  6mm |
| .  | .  |  32  | .  | 4  | .  | .  | 36  |  Bolt M3 caphead x 10mm |
| .  | .  | .  | .  | .  | .  | 2  | 2  |  Bolt M3 caphead x 12mm |
| .  | .  | 2  | 2  | .  | .  | .  | 4  |  Bolt M3 caphead x 16mm |
| .  | .  | 3  | .  | .  | .  | 4  | 7  |  Bolt M3 caphead x 25mm |
| .  | .  | 1  | .  | .  | .  | .  | 1  |  Bolt M3 caphead x 35mm |
| .  | 2  | .  | .  | .  | .  | .  | 2  |  Bolt M3 caphead x 40mm |
| .  | .  | 2  | .  | 2  | .  | 2  | 6  |  Bolt M3 countersunk x 10mm |
| .  | .  | 4  | .  | .  | .  | 2  | 6  |  Bolt M3 countersunk x 12mm |
| 2  | .  | .  | .  | .  | .  | .  | 2  |  Bolt M3 countersunk x 25mm |
| .  | .  | 4  | .  | .  | .  | .  | 4  |  Bolt M3 countersunk x 35mm |
| .  | .  | .  | .  | .  | .  | 4  | 4  |  Bolt M3 countersunk x 40mm |
| .  | .  | .  | 8  | .  | .  |  55  | 63  |  Bolt M4 buttonhead x  8mm |
| .  | .  |  12  | .  | 6  | 4  |  14  | 36  |  Bolt M4 buttonhead x 10mm |
| .  | .  | 8  | .  | .  | .  | 4  | 12  |  Bolt M4 buttonhead x 12mm |
| .  | .  |  20  | .  | .  | 8  | .  | 28  |  Bolt M4 countersunk x 10mm |
| .  | .  | .  | .  | 4  | .  | .  | 4  |  Bolt M4 countersunk x 45mm |
| .  | .  | 6  | .  | .  | .  | .  | 6  |  Bolt M5 buttonhead x 10mm |
| .  | .  |  14  | 8  | 8  | 8  |  14  | 52  |  Bolt M5 buttonhead x 12mm |
| .  | .  | .  | .  | 4  | .  | .  | 4  |  Bolt M5 buttonhead x 16mm |
| .  | .  | .  | .  | 4  | .  | .  | 4  |  Bolt M5 countersunk x 12mm |
| .  | .  | 2  | 1  | .  | .  | 1  | 4  |  Cork damper NEMA 17 |
| .  | .  | .  | .  | 2  | .  | .  | 2  |  Extrusion E2020 x 300mm |
| .  | .  | .  | .  | .  | .  | 1  | 1  |  Extrusion E2020 x 350mm |
| .  | .  | .  | 2  | .  | 2  | .  | 4  |  Extrusion E2020 x 400mm |
| .  | .  | .  | .  | 2  | .  | .  | 2  |  Extrusion E2040 x 150mm |
| .  | .  | 2  | 2  | .  | 2  | 1  | 7  |  Extrusion E2040 x 350mm |
| .  | .  | 2  | .  | .  | .  | .  | 2  |  Extrusion E2060 x 350mm |
| .  | .  | .  | .  | .  | .  | 1  | 1  |  Extrusion E2080 x 350mm |
| 1  | .  | .  | .  | .  | .  | .  | 1  |  Fan 30mm x 10mm |
| .  | .  | .  | 1  | .  | .  | .  | 1  |  Filament sensor |
| .  | .  | .  | .  | 1  | .  | .  | 1  |  Heated Bed 235mm x 235mm |
| .  | .  | .  | .  | 4  | .  | .  | 4  |  Heated bed leveling knob |
| .  | .  | 4  | .  | .  | .  | .  | 4  |  Heatfit insert M3 |
| 1  | .  | .  | .  | .  | .  | .  | 1  |  Hot end E3D V6 direct 1.75mm |
| .  | .  | .  | .  | .  | .  | 1  | 1  |  IEC320 C14 switched fused inlet module |
| .  | .  | .  | .  | 1  | .  | .  | 1  |  Leadscrew nut 8 x 2 |
| .  | .  | 1  | .  | .  | .  | .  | 1  |  Linear rail MGN12 x 300mm |
| .  | .  | 2  | .  | .  | .  | .  | 2  |  Linear rail MGN12 x 350mm |
| .  | .  | 3  | .  | .  | .  | .  | 3  |  Linear rail carriage MGN12H |
| .  | .  | .  | .  | .  | .  | 2  | 2  |  Linear rod 12mm x 300mm |
| .  | .  | .  | 1  | .  | .  | .  | 1  |  MK10 Dual Pulley Extruder |
| .  | .  | .  | .  | .  | .  | 1  | 1  |  Micro SD card |
| .  | .  |  20  | .  | 2  | .  | 6  | 28  |  Nut M3 hammer |
| .  | .  |  12  | 8  | .  | .  |  69  | 89  |  Nut M4 hammer |
| .  | .  |  36  | .  | 6  |  12  | .  | 54  |  Nut M4 sliding T |
| .  | .  | .  | .  | .  | .  | 1  | 1  |  PSU NIUGUY CB-500W-24V |
| .  | .  | .  | .  | .  | .  | 1  | 1  |  PTFE Bowden tube, 600 mm |
| .  | .  | .  | .  | .  | .  |  12  | 12  |  Pillar hex nylon F/F M3x10 |
| .  | .  | .  | 2  | .  | .  | .  | 2  |  Pillar hex nylon F/F M3x14 |
| .  | .  | .  | .  | .  | .  | 2  | 2  |  Pillar hex nylon F/F M3x25 |
| .  | .  | .  | .  | .  | .  | 2  | 2  |  Pillar hex nylon F/F M3x5 |
| .  | .  | 2  | .  | .  | .  | .  | 2  |  Pulley GT2OB 20 teeth |
| .  | .  | .  | .  | .  | .  | 1  | 1  |  Raspberry Pi 3A+ |
| .  | .  | 1  | .  | .  | .  | .  | 1  |  Raspberry Pi camera V2 |
| .  | .  | .  | .  | 2  | .  | .  | 2  |  SCS12LUU bearing block |
| .  | .  | .  | .  | .  | 4  | .  | 4  |  SK12 shaft support bracket |
| .  | .  | .  | .  | .  | .  | 1  | 1  |  Sheet polycarbonate 295mm x 400mm x 3mm |
| .  | .  | .  | .  | .  | .  | 2  | 2  |  Sheet polycarbonate 390mm x 400mm x 3mm |
| .  | .  | .  | .  | 4  | .  | .  | 4  |  Spring 8mm OD, 0.9mm gauge x 20mm long, closed end |
| 1  | .  | .  | .  | .  | .  | .  | 1  |  Square radial fan 3010 |
| .  | .  | .  | .  | .  | .  | 1  | 1  |  Stepper motor NEMA17 x 40mm, 280mm integrated leadscrew |
| .  | .  | 2  | 1  | .  | .  | .  | 3  |  Stepper motor NEMA17 x 47mm |
| .  | .  | .  | 1  | .  | .  | .  | 1  |  Stepper motor cable, 200mm |
| .  | .  | 1  | .  | .  | .  | .  | 1  |  Stepper motor cable, 300mm |
| .  | .  | 1  | .  | .  | .  | .  | 1  |  Stepper motor cable, 500mm |
| .  | .  | .  | .  | .  | .  | 1  | 1  |  Stepper motor cable, 850mm |
| .  | 2  |  38  | .  | .  | .  | .  | 40  |  Washer M3 |
| .  | .  | .  | .  | .  | .  | 1  | 1  |  XL4015 buck converter |
| 3  | .  | .  | .  | .  | .  | .  | 3  |  Ziptie 2.5mm x 100mm min length |
|  12  | 4  | 281  |  39  |  58  |  40  | 251  |  685  | Total vitamins count |
| | | | | | | | | **3D printed parts** |
| .  | .  | 1  | .  | .  | .  | .  | 1  | Camera_Mount.stl |
| .  | .  | .  | .  | .  | .  | 1  | 1  | Display_Housing_Bracket_TFT35_E3.stl |
| .  | .  | .  | .  | .  | .  | 1  | 1  | Display_Housing_TFT35_E3.stl |
| .  | .  | .  | 1  | .  | .  | .  | 1  | Extruder_Bracket.stl |
| 1  | .  | .  | .  | .  | .  | .  | 1  | Fan_Duct.stl |
| .  | .  | .  | .  | .  | .  | 4  | 4  | Foot_LShaped_12mm.stl |
| .  | .  | .  | .  | .  | .  | 1  | 1  | Front_Cover_350.stl |
| .  | .  | .  | .  | .  | .  | 1  | 1  | Front_Display_Wiring_Cover_350.stl |
| .  | .  | 2  | .  | .  | .  | .  | 2  | Handle.stl |
| 1  | .  | .  | .  | .  | .  | .  | 1  | Hotend_Clamp.stl |
| .  | .  | .  | .  | .  | .  | 1  | 1  | IEC_Housing.stl |
| .  | .  | .  | .  | .  | .  | 1  | 1  | IEC_Housing_Mount.stl |
| .  | .  | .  | .  | 1  | .  | .  | 1  | Printbed_Strain_Relief.stl |
| .  | .  | .  | .  | 1  | .  | .  | 1  | Printbed_Strain_Relief_Clamp.stl |
| .  | .  | .  | 1  | .  | .  | .  | 1  | Right_Side_Panel.stl |
| .  | .  | .  | .  | .  | .  | 1  | 1  | Spool_Holder.stl |
| .  | .  | .  | .  | .  | .  | 1  | 1  | Spool_Holder_36.stl |
| .  | .  | .  | .  | .  | .  | 1  | 1  | Spool_Holder_Bracket.stl |
| .  | .  | 4  | .  | .  | .  | .  | 4  | Top_Corner_Piece.stl |
| .  | .  | .  | .  | .  | .  | 1  | 1  | Wiring_Guide.stl |
| .  | .  | .  | .  | .  | .  | 1  | 1  | Wiring_Guide_Clamp.stl |
| .  | .  | 1  | .  | .  | .  | .  | 1  | Wiring_Guide_Socket.stl |
| .  | .  | 1  | .  | .  | .  | .  | 1  | XY_Idler_Left_RB_40.stl |
| .  | .  | 1  | .  | .  | .  | .  | 1  | XY_Idler_Right_RB_40.stl |
| .  | .  | 1  | .  | .  | .  | .  | 1  | XY_Motor_Mount_Brace_Left_RB.stl |
| .  | .  | 1  | .  | .  | .  | .  | 1  | XY_Motor_Mount_Brace_Right_RB.stl |
| .  | .  | 1  | .  | .  | .  | .  | 1  | XY_Motor_Mount_Left_RB.stl |
| .  | .  | 2  | .  | .  | .  | .  | 2  | XY_Motor_Mount_Pulley_Spacer.stl |
| .  | .  | 1  | .  | .  | .  | .  | 1  | XY_Motor_Mount_Right_RB.stl |
| .  | .  | 1  | .  | .  | .  | .  | 1  | X_Carriage_Belt_Clamp.stl |
| .  | 1  | .  | .  | .  | .  | .  | 1  | X_Carriage_Belt_Side_RB.stl |
| .  | 2  | .  | .  | .  | .  | .  | 2  | X_Carriage_Belt_Tensioner_RB.stl |
| 1  | .  | .  | .  | .  | .  | .  | 1  | X_Carriage_Groovemount.stl |
| .  | .  | 1  | .  | .  | .  | .  | 1  | Y_Carriage_Brace_Left_RB.stl |
| .  | .  | 1  | .  | .  | .  | .  | 1  | Y_Carriage_Brace_Right_RB.stl |
| .  | .  | 1  | .  | .  | .  | .  | 1  | Y_Carriage_Left_RB.stl |
| .  | .  | 1  | .  | .  | .  | .  | 1  | Y_Carriage_Right_RB.stl |
| .  | .  | .  | .  | 1  | .  | .  | 1  | Z_Carriage_Center.stl |
| .  | .  | .  | .  | 2  | .  | .  | 2  | Z_Carriage_Side.stl |
| .  | .  | .  | .  | .  | 1  | .  | 1  | Z_Motor_Mount.stl |
| .  | .  | .  | .  | .  | 1  | .  | 1  | Z_Motor_MountGuide_61mm.stl |
| .  | .  | .  | .  | .  | 2  | .  | 2  | Z_RodMountGuide_40mm.stl |
| 3  | 3  |  21  | 2  | 5  | 4  |  15  | 53  | Total 3D printed parts count |
| | | | | | | | | **CNC routed parts** |
| .  | .  | .  | .  | .  | .  | 1  | 1  | Back_Panel.dxf |
| .  | .  | .  | .  | .  | .  | 1  | 1  | BaseAL.dxf |
| .  | .  | .  | .  | .  | .  | 1  | 1  | Left_Side_Panel.dxf |
| .  | .  | .  | .  | .  | .  | 1  | 1  | Right_Side_Panel.dxf |
| .  | .  | .  | .  | .  | .  | 4  | 4  | Total CNC routed parts count |

<span></span>
[Top](#TOP)

---

## Printhead_E3DV6 assembly

### Vitamins

| Qty | Description |
|----:|:---|
| 4 | Bolt M2 caphead x  6mm |
| 2 | Bolt M3 countersunk x 25mm |
| 1 | Fan 30mm x 10mm |
| 1 | Hot end E3D V6 direct 1.75mm |
| 1 | Square radial fan 3010 |
| 3 | Ziptie 2.5mm x 100mm min length |

### 3D Printed parts

| 1 x Fan_Duct.stl | 1 x Hotend_Clamp.stl | 1 x X_Carriage_Groovemount.stl |
|---|---|---|
| Fan_Duct.stl | Hotend_Clamp.stl | X_Carriage_Groovemount.stl |

### Assembly instructions

Printhead_E3DV6_assembly

1. Bolt the fan onto the side of the **X_Carriage_Groovemount**, secure the fan wire with a ziptie.
2. Ensure a good fit between the fan and the **Fan_Duct** and bolt the fan duct to the X_Carriage.
3. Assemble the E3D hotend, including fan, thermistor cartridge and heater cartridge.
4. Use the **Hotend_Clamp** to attach the E3D hotend to the X_Carriage.
5. Collect the wires together, wrap them in spiral wrap, and secure them to the X_Carriage using the zipties. Note that
the wiring is not shown in this diagram.

Printhead_E3DV6_assembled

<span></span>
[Top](#TOP)

---

## X_Carriage_Belt_Side assembly

### Vitamins

| Qty | Description |
|----:|:---|
| 2 | Bolt M3 caphead x 40mm |
| 2 | Washer M3 |

### 3D Printed parts

| 1 x X_Carriage_Belt_Side_RB.stl | 2 x X_Carriage_Belt_Tensioner_RB.stl |
|---|---|
| X_Carriage_Belt_Side_RB.stl | X_Carriage_Belt_Tensioner_RB.stl |

### Assembly instructions

X_Carriage_Belt_Side_assembly

Insert the belts into the **X_Carriage_Belt_Tensioner**s and then bolt the tensioners into the
**X_Carriage_Belt_Side** part as shown. Note the belts are not shown in this diagram.

X_Carriage_Belt_Side_assembled

<span></span>
[Top](#TOP)

---

## XY_Motor_Mount_Right assembly

### Vitamins

| Qty | Description |
|----:|:---|
| 6 | Ball bearing F623-2RS 3mm x 10mm x 4mm |
| 6 | Bolt M3 buttonhead x 10mm |
| 2 | Bolt M3 countersunk x 35mm |
| 3 | Bolt M4 buttonhead x 10mm |
| 1 | Cork damper NEMA 17 |
| 3 | Nut M4 hammer |
| 1 | Pulley GT2OB 20 teeth |
| 1 | Stepper motor NEMA17 x 47mm |
| 1 | Stepper motor cable, 300mm |
|  11 | Washer M3 |

### 3D Printed parts

| 1 x XY_Motor_Mount_Brace_Right_RB.stl | 1 x XY_Motor_Mount_Pulley_Spacer.stl | 1 x XY_Motor_Mount_Right_RB.stl |
|---|---|---|
| XY_Motor_Mount_Brace_Right_RB.stl | XY_Motor_Mount_Pulley_Spacer.stl | XY_Motor_Mount_Right_RB.stl |

### Assembly instructions

XY_Motor_Mount_Right_assembly

1. Bolt the idler pulleys and the **XY_Motor_Mount_Brace_Right** to the **XY_Motor_Mount_Right**. Note the brace is not
symmetrical - there is an orientation indicator and this should point towards the back of the printer. Tighten the
pulley bolts until the pulleys no longer turn freely, and then loosen the bolts by about 1/4 turn until the pulleys
turn freely again.
2. Bolt the motor and the cork damper to the motor mount. The core damper thermally insulates the motor from the mount
and should not be omitted.
3. Align the drive pulley with the idler pulleys and bolt it to the motor shaft.
4. Add the bolts and t-nuts in preparation for later attachment to the frame.

XY_Motor_Mount_Right_assembled

<span></span>
[Top](#TOP)

---

## XY_Motor_Mount_Left assembly

### Vitamins

| Qty | Description |
|----:|:---|
| 6 | Ball bearing F623-2RS 3mm x 10mm x 4mm |
| 6 | Bolt M3 buttonhead x 10mm |
| 2 | Bolt M3 countersunk x 35mm |
| 3 | Bolt M4 buttonhead x 10mm |
| 1 | Cork damper NEMA 17 |
| 3 | Nut M4 hammer |
| 1 | Pulley GT2OB 20 teeth |
| 1 | Stepper motor NEMA17 x 47mm |
| 1 | Stepper motor cable, 500mm |
|  11 | Washer M3 |

### 3D Printed parts

| 1 x XY_Motor_Mount_Brace_Left_RB.stl | 1 x XY_Motor_Mount_Left_RB.stl | 1 x XY_Motor_Mount_Pulley_Spacer.stl |
|---|---|---|
| XY_Motor_Mount_Brace_Left_RB.stl | XY_Motor_Mount_Left_RB.stl | XY_Motor_Mount_Pulley_Spacer.stl |

### Assembly instructions

XY_Motor_Mount_Left_assembly

1. Bolt the idler pulleys and the **XY_Motor_Mount_Brace_Left** to the **XY_Motor_Mount_Left**. Note the brace is not
symmetrical - there is an orientation indicator and this should point towards the back of the printer. Tighten the
pulley bolts until the pulleys no longer turn freely, and then loosen the bolts by about 1/4 turn until the pulleys
turn freely again.
2. Bolt the motor and the cork damper to the motor mount. The core damper thermally insulates the motor from the mount
and should not be omitted.
3. Align the drive pulley with the idler pulleys and bolt it to the motor shaft.
4. Add the bolts and t-nuts in preparation for later attachment to the frame.

XY_Motor_Mount_Left_assembled

<span></span>
[Top](#TOP)

---

## XY_Idler_Right assembly

### Vitamins

| Qty | Description |
|----:|:---|
| 2 | Ball bearing F623-2RS 3mm x 10mm x 4mm |
| 1 | Bolt M3 caphead x 25mm |
| 2 | Bolt M4 buttonhead x 10mm |
| 1 | Nut M3 hammer |
| 2 | Nut M4 hammer |
| 3 | Washer M3 |

### 3D Printed parts

| 1 x XY_Idler_Right_RB_40.stl |
|----------|
| XY_Idler_Right_RB_40.stl |

### Assembly instructions

XY_Idler_Right_assembly

1. Bolt the pulley stack into the **XY_Idler_Right**. Note that there are 4 washers between the two pulleys and one
washer at the top and the bottom of the pulley stack.
2. Tighten the bolt until the pulleys no longer turn freely, and then loosen the bolt by about 1/4 turn to allow the pulleys
to turn freely again.
3. Add the bolts and t-nuts in preparation for later attachment to the frame.
4. Add the button head bolt and washer.

XY_Idler_Right_assembled

<span></span>
[Top](#TOP)

---

## XY_Idler_Left assembly

### Vitamins

| Qty | Description |
|----:|:---|
| 2 | Ball bearing F623-2RS 3mm x 10mm x 4mm |
| 1 | Bolt M3 caphead x 35mm |
| 2 | Bolt M4 buttonhead x 10mm |
| 1 | Nut M3 hammer |
| 2 | Nut M4 hammer |
| 3 | Washer M3 |

### 3D Printed parts

| 1 x XY_Idler_Left_RB_40.stl |
|----------|
| XY_Idler_Left_RB_40.stl |

### Assembly instructions

XY_Idler_Left_assembly

1. Bolt the pulley stack into the **XY_Idler_Left**. Note that there are 4 washers between the two pulleys and one
washer at the top and the bottom of the pulley stack.
2. Tighten the bolt until the pulleys no longer turn freely, and then loosen the bolt by about 1/4 turn to allow the pulleys
to turn freely again.
3. Add the bolts and t-nuts in preparation for later attachment to the frame.
4. Add the button head bolt and washer.

XY_Idler_Left_assembled

<span></span>
[Top](#TOP)

---

## Y_Carriage_Right assembly

### Vitamins

| Qty | Description |
|----:|:---|
| 4 | Ball bearing F623-2RS 3mm x 10mm x 4mm |
| 2 | Bolt M3 caphead x 10mm |
| 1 | Bolt M3 caphead x 16mm |
| 1 | Bolt M3 caphead x 25mm |
| 2 | Heatfit insert M3 |
| 5 | Washer M3 |

### 3D Printed parts

| 1 x Y_Carriage_Brace_Right_RB.stl | 1 x Y_Carriage_Right_RB.stl |
|---|---|
| Y_Carriage_Brace_Right_RB.stl | Y_Carriage_Right_RB.stl |

### Assembly instructions

Y_Carriage_Right_assembly

1. Insert the threaded inserts into the **Y_Carriage_Right** as shown.
2. Drive a long M3 bolt through the Y carriage from the insert side to self tap the part of the hole after the insert.
Once this hole is tapped, remove the bolt.
3. Bolt the **Y_Carriage_Brace_Right** and the pulleys to the **Y_Carriage_Right** as shown. Note the position of the washers.
4. Tighten the bolts until the pulleys no longer turn freely and then loosen by about 1/4 turn so the pulleys can again turn.

Y_Carriage_Right_assembled

<span></span>
[Top](#TOP)

---

## Right_Side_Upper_Extrusion assembly

### Vitamins

| Qty | Description |
|----:|:---|
|  12 | Bolt M3 caphead x 10mm |
| 6 | Bolt M5 buttonhead x 12mm |
| 1 | Extrusion E2060 x 350mm |
| 1 | Linear rail MGN12 x 350mm |
| 1 | Linear rail carriage MGN12H |
| 8 | Nut M3 hammer |

### Sub-assemblies

| 1 x Y_Carriage_Right_assembly |
|----------|
| Y_Carriage_Right_assembled |

### Assembly instructions

Right_Side_Upper_Extrusion_assembly

1. Bolt the MGN linear rail to the extrusion, using the **Rail_Centering_Jig** to align the rail. Do not fully tighten the
bolts at this stage - they will be fully tightened when the rail is racked at a later stage.
2. Bolt the **Y_Carriage_Right_assembly** to the MGN carriage.
3. Screw the bolts into ends of the extrusion in preparation for attachment to the rest of the top face.

Right_Side_Upper_Extrusion_assembled

<span></span>
[Top](#TOP)

---

## Y_Carriage_Left assembly

### Vitamins

| Qty | Description |
|----:|:---|
| 4 | Ball bearing F623-2RS 3mm x 10mm x 4mm |
| 2 | Bolt M3 caphead x 10mm |
| 1 | Bolt M3 caphead x 16mm |
| 1 | Bolt M3 caphead x 25mm |
| 2 | Heatfit insert M3 |
| 5 | Washer M3 |

### 3D Printed parts

| 1 x Y_Carriage_Brace_Left_RB.stl | 1 x Y_Carriage_Left_RB.stl |
|---|---|
| Y_Carriage_Brace_Left_RB.stl | Y_Carriage_Left_RB.stl |

### Assembly instructions

Y_Carriage_Left_assembly

1. Insert the threaded inserts into the **Y_Carriage_Left** as shown.
2. Drive a long M3 bolt through the Y carriage from the insert side to self tap the part of the hole after the insert.
Once this hole is tapped, remove the bolt.
3. Bolt the **Y_Carriage_Brace_Left** and the pulleys to the **Y_Carriage_Left** as shown. Note the position of the washers.
4. Tighten the bolts until the pulleys no longer turn freely and then loosen by about 1/4 turn so the pulleys can again turn.

Y_Carriage_Left_assembled

<span></span>
[Top](#TOP)

---

## Left_Side_Upper_Extrusion assembly

### Vitamins

| Qty | Description |
|----:|:---|
|  12 | Bolt M3 caphead x 10mm |
| 6 | Bolt M5 buttonhead x 12mm |
| 1 | Extrusion E2060 x 350mm |
| 1 | Linear rail MGN12 x 350mm |
| 1 | Linear rail carriage MGN12H |
| 8 | Nut M3 hammer |

### Sub-assemblies

| 1 x Y_Carriage_Left_assembly |
|----------|
| Y_Carriage_Left_assembled |

### Assembly instructions

Left_Side_Upper_Extrusion_assembly

1. Bolt the MGN linear rail to the extrusion, using the **Rail_Centering_Jig** to align the rail. Fully tighten the
bolts - the left rail is the fixed rail and the right rail will be aligned to it.
bolts at this stage - they will be fully tightened when the rail is racked at a later stage.
2. Bolt the **Y_Carriage_Left_assembly** to the MGN carriage.
3. Screw the bolts into ends of the extrusion in preparation for attachment to the rest of the top face.

Left_Side_Upper_Extrusion_assembled

<span></span>
[Top](#TOP)

---

## Face_Top_Stage_1 assembly

### Vitamins

| Qty | Description |
|----:|:---|
| 4 | Bolt M2 caphead x  8mm |
| 2 | Bolt M3 buttonhead x 10mm |
| 2 | Bolt M4 buttonhead x 10mm |
|  20 | Bolt M4 countersunk x 10mm |
| 6 | Bolt M5 buttonhead x 10mm |
| 2 | Bolt M5 buttonhead x 12mm |
| 2 | Extrusion E2040 x 350mm |
| 2 | Nut M3 hammer |
| 2 | Nut M4 hammer |
|  28 | Nut M4 sliding T |
| 1 | Raspberry Pi camera V2 |

### 3D Printed parts

| 1 x Camera_Mount.stl | 4 x Top_Corner_Piece.stl | 1 x Wiring_Guide_Socket.stl |
|---|---|---|
| Camera_Mount.stl | Top_Corner_Piece.stl | Wiring_Guide_Socket.stl |

### Sub-assemblies

| 1 x Left_Side_Upper_Extrusion_assembly | 1 x Right_Side_Upper_Extrusion_assembly | 1 x XY_Idler_Left_assembly |
|---|---|---|
| Left_Side_Upper_Extrusion_assembled | Right_Side_Upper_Extrusion_assembled | XY_Idler_Left_assembled |
| 1 x XY_Idler_Right_assembly | 1 x XY_Motor_Mount_Left_assembly | 1 x XY_Motor_Mount_Right_assembly |
|----------|----------|----------|
| XY_Idler_Right_assembled | XY_Motor_Mount_Left_assembled | XY_Motor_Mount_Right_assembled |

### Assembly instructions

Face_Top_Stage_1_assembly

1. Bolt the two motor mounts, the **Wiring_Guide**, and optionally the **Camera_Mount** to the rear extrusion.
2. Bolt the two idlers to the front extrusion.
3. Screw the bolts into the ends of the front and rear extrusions.
4. Insert the t-nuts for the **Handle** into the extrusions.
5. Insert the t-nuts for the **Top_Corner_Piece**s into the extrusions.
6. Bolt the front and rear extrusions to the side extrusions, leaving the bolts slightly loose.
7. Bolt the **Top_Corner_Piece**s to the extrusions leaving the bolts slightly loose.
8. Turn the top face upside down and place on a flat surface. Ensure it is square and tighten the hidden bolts.
9. Turn the top face the right way up and tighten the bolts on the **Top_Corner_Piece**s.

Face_Top_Stage_1_assembled

<span></span>
[Top](#TOP)

---

## Face_Top_Stage_2 assembly

### Vitamins

| Qty | Description |
|----:|:---|
| 4 | Bolt M3 caphead x 10mm |
| 1 | Linear rail MGN12 x 300mm |
| 1 | Linear rail carriage MGN12H |

### Sub-assemblies

| 1 x Face_Top_Stage_1_assembly |
|----------|
| Face_Top_Stage_1_assembled |

### Assembly instructions

Face_Top_Stage_2_assembly

1. Bolt the MGN rail to the Y_Carriages as shown. Ensure the MGN rail is square to the frame.
2. Turn the top face upside down and place on a flat surface. Rack the right side linear rail - move the X-rail
to one extreme of the frame and tighten the bolts on that end of the Y-rail. Then move the X-rail to the other
extreme and tighten the bolts on that end of the Y-rail. Finally tighten the remaining bolts on the Y-rail.
3. Ensure the X-rail moves freely, if it doesn't loosen the bolts you have just tightened and repeat step 2.

Face_Top_Stage_2_assembled

<span></span>
[Top](#TOP)

---

## Face_Top assembly

### Vitamins

| Qty | Description |
|----:|:---|
| 1 | Belt GT2 x 6mm x 1476mm |
| 1 | Belt GT2 x 6mm x 1500mm |
| 2 | Bolt M3 countersunk x 10mm |
| 4 | Bolt M3 countersunk x 12mm |
| 8 | Bolt M4 buttonhead x 12mm |
| 8 | Nut M4 sliding T |

### 3D Printed parts

| 2 x Handle.stl | 1 x X_Carriage_Belt_Clamp.stl |
|---|---|
| Handle.stl | X_Carriage_Belt_Clamp.stl |

### Sub-assemblies

| 1 x Face_Top_Stage_2_assembly | 1 x X_Carriage_Belt_Side_assembly |
|---|---|
| Face_Top_Stage_2_assembled | X_Carriage_Belt_Side_assembled |

### Assembly instructions

Face_Top_assembly

1. Bolt the **X_Carriage_Belt_Side_assembly** to the MGN carriage.
2. Thread the belts as shown and attach them to the **X_Carriage_Belt_Side_assembly**
using the **X_Carriage_Belt_Clamp**.
3. Leave the belts fairly loose - tensioning of the belts is done after the frame is assembled.
4. Bolt the handles to the previously inserted t-nuts.

Face_Top_assembled

<span></span>
[Top](#TOP)

---

## Extruder_Bracket assembly

### Vitamins

| Qty | Description |
|----:|:---|
| 2 | Bolt M3 buttonhead x 10mm |
| 2 | Bolt M3 caphead x 16mm |
| 4 | Bolt M4 buttonhead x  8mm |
| 1 | Cork damper NEMA 17 |
| 1 | Filament sensor |
| 1 | MK10 Dual Pulley Extruder |
| 4 | Nut M4 hammer |
| 2 | Pillar hex nylon F/F M3x14 |
| 1 | Stepper motor NEMA17 x 47mm |
| 1 | Stepper motor cable, 200mm |

### 3D Printed parts

| 1 x Extruder_Bracket.stl |
|----------|
| Extruder_Bracket.stl |

### Assembly instructions

Extruder_Bracket_assembly

1. Bolt the stepper motor and cork damper through the **Extruder_Bracket** to the extruder as shown. The cork damper
thermally isolates the motor from the **Extruder_Bracket** and should not be omitted.
2. Align the hobb gear on the stepper motor shaft with the the hobb gear in the extruder and tighten the grub screws.
3. Bolt the filament sensor to the hex pillars and bolt them to the **Extruder_Bracket**.
4. Add the bolts and t-nuts in preparation for later attachment to the frame.

Extruder_Bracket_assembled

<span></span>
[Top](#TOP)

---

## Right_Side assembly

### Vitamins

| Qty | Description |
|----:|:---|
| 4 | Bolt M4 buttonhead x  8mm |
| 8 | Bolt M5 buttonhead x 12mm |
| 2 | Extrusion E2020 x 400mm |
| 2 | Extrusion E2040 x 350mm |
| 4 | Nut M4 hammer |

### 3D Printed parts

| 1 x Right_Side_Panel.stl |
|----------|
| Right_Side_Panel.stl |

### Sub-assemblies

| 1 x Extruder_Bracket_assembly |
|----------|
| Extruder_Bracket_assembled |

### Assembly instructions

Right_Side_assembly

1. On a flat surface, bolt the upper and lower extrusions into the left and right uprights as shown.
2. Bolt the **IEC_Housing_assembly** to the lower extrusion and upright.
3. Bolt the **Extruder_Bracket_assembly** to the upper extrusion and upright.

Right_Side_assembled

<span></span>
[Top](#TOP)

---

## Display_Cover_TFT35_E3 assembly

### Vitamins

| Qty | Description |
|----:|:---|
| 1 | BigTreeTech TFT35 E3 v3.0 |
| 4 | Bolt M3 caphead x  6mm |

### 3D Printed parts

| 1 x Display_Housing_TFT35_E3.stl |
|----------|
| Display_Housing_TFT35_E3.stl |

### Assembly instructions

Display_Cover_TFT35_E3_assembly

1. Bolt the TFT35 E3 display to the **Display_Housing_TFT35_E3**.
2. Attach the knob to the display.

Display_Cover_TFT35_E3_assembled

<span></span>
[Top](#TOP)

---

## IEC_Housing assembly

### Vitamins

| Qty | Description |
|----:|:---|
| 5 | Bolt M4 buttonhead x  8mm |
| 2 | Bolt M4 buttonhead x 12mm |
| 1 | IEC320 C14 switched fused inlet module |
| 5 | Nut M4 hammer |

### 3D Printed parts

| 1 x IEC_Housing.stl | 1 x IEC_Housing_Mount.stl |
|---|---|
| IEC_Housing.stl | IEC_Housing_Mount.stl |

### Assembly instructions

IEC_Housing_assembly

1. Attach the power cables to the IEC connector.
2. Thread the power cables through the hole in the **IEC_Housing** and bolt the **IEC_Housing_Mount** to the **IEC_housing**.
3. Add the bolts and t-nuts in preparation for attachment to the frame.

IEC_Housing_assembled

<span></span>
[Top](#TOP)

---

## Base_Plate_Stage_1 assembly

### Vitamins

| Qty | Description |
|----:|:---|
| 1 | Aluminium sheet 390mm x 390mm x 3mm |
| 1 | BigTreeTech Relay Module v1.2 |
| 1 | BigTreeTech SKR v1.4 Turbo |
|  14 | Bolt M3 buttonhead x 10mm |
|  14 | Bolt M3 caphead x  6mm |
| 2 | Bolt M3 caphead x 12mm |
| 8 | Bolt M4 buttonhead x  8mm |
|  10 | Bolt M4 buttonhead x 10mm |
|  14 | Bolt M5 buttonhead x 12mm |
| 1 | Extrusion E2020 x 350mm |
| 1 | Extrusion E2040 x 350mm |
| 1 | Extrusion E2080 x 350mm |
| 1 | Micro SD card |
| 2 | Nut M3 hammer |
|  16 | Nut M4 hammer |
| 1 | PSU NIUGUY CB-500W-24V |
|  12 | Pillar hex nylon F/F M3x10 |
| 2 | Pillar hex nylon F/F M3x25 |
| 2 | Pillar hex nylon F/F M3x5 |
| 1 | Raspberry Pi 3A+ |
| 1 | XL4015 buck converter |

### 3D Printed parts

| 4 x Foot_LShaped_12mm.stl |
|----------|
| Foot_LShaped_12mm.stl |

### CNC Routed parts

| 1 x BaseAL.dxf |
|----------|
| BaseAL.dxf |

### Sub-assemblies

| 1 x IEC_Housing_assembly |
|----------|
| IEC_Housing_assembled |

### Assembly instructions

Base_Plate_Stage_1_assembly

If you have access to a CNC, you can machine the base plate using **BaseAL.dxf**, if not you can use the **Panel_Jig**
as a template to drill the holes in the base plate.

1. Insert the bolts into the ends of the E2040 and E2080 extrusions in preparation for connection to the frame uprights.
2. Bolt the extrusions and the L-shaped feet to the baseplate as shown.
3. Bolt the PSU and the pcbs to the baseplate, using standoffs as appropriate.

Base_Plate_Stage_1_assembled

<span></span>
[Top](#TOP)

---

## Base_Plate assembly

### Vitamins

| Qty | Description |
|----:|:---|
| 4 | Bolt M3 caphead x 25mm |
| 2 | Bolt M3 countersunk x 10mm |
| 2 | Bolt M3 countersunk x 12mm |
| 4 | Bolt M4 buttonhead x 10mm |
| 4 | Nut M3 hammer |
| 4 | Nut M4 hammer |

### 3D Printed parts

| 1 x Display_Housing_Bracket_TFT35_E3.stl | 1 x Front_Cover_350.stl | 1 x Front_Display_Wiring_Cover_350.stl |
|---|---|---|
| Display_Housing_Bracket_TFT35_E3.stl | Front_Cover_350.stl | Front_Display_Wiring_Cover_350.stl |

### Sub-assemblies

| 1 x Base_Plate_Stage_1_assembly | 1 x Display_Cover_TFT35_E3_assembly |
|---|---|
| Base_Plate_Stage_1_assembled | Display_Cover_TFT35_E3_assembled |

### Assembly instructions

Base_Plate_assembly

1. Bolt the **Display_Housing_Bracket_TFT35_E3** to the 2080 extrusion.
2. Thread the display wiring through the hole in the **Display_Housing_Bracket_TFT35_E3** and connect it to the TFT display.
3. Bolt the **Display_Cover_TFT35_E3_assembly** to the **Display_Housing_Bracket_TFT35_E3**.
4. Bolt the **Front_Cover** to the top of the 2080 extrusion.
5. Bolt the **Front_Display_Wiring_Cover** to the top of the 2080 extrusion, covering the wiring.
6. Route the wiring to the back of the base, ready for later connection to the mainboard.

Base_Plate_assembled

<span></span>
[Top](#TOP)

---

## 2 x Z_Carriage_Side assembly

### Vitamins

| Qty | Description |
|----:|:---|
| 2 | Bolt M4 buttonhead x 10mm |
| 4 | Bolt M5 buttonhead x 16mm |
| 4 | Bolt M5 countersunk x 12mm |
| 2 | Nut M4 sliding T |
| 2 | SCS12LUU bearing block |

### 3D Printed parts

| 2 x Z_Carriage_Side.stl |
|----------|
| Z_Carriage_Side.stl |

### Assembly instructions

Z_Carriage_Side_assembly

1. Bolt the SCS bearing block to the **Z_Carriage**.
2. Add the bolts and t-nuts in preparation for connection to the printbed.

Z_Carriage_Side_assembled

<span></span>
[Top](#TOP)

---

## Z_Carriage_Center assembly

### Vitamins

| Qty | Description |
|----:|:---|
| 4 | Bolt M3 caphead x 10mm |
| 4 | Bolt M4 buttonhead x 10mm |
| 1 | Leadscrew nut 8 x 2 |
| 4 | Nut M4 sliding T |

### 3D Printed parts

| 1 x Z_Carriage_Center.stl |
|----------|
| Z_Carriage_Center.stl |

### Assembly instructions

Z_Carriage_Center_assembly

1. Bolt the leadscrew to the **Z_Carriage_Center**.
2. Add the bolts and t-nuts in preparation for later attachment to the printbed frame.

Z_Carriage_Center_assembled

<span></span>
[Top](#TOP)

---

## Printbed_Frame assembly

### Vitamins

| Qty | Description |
|----:|:---|
| 2 | Bolt M3 countersunk x 10mm |
| 8 | Bolt M5 buttonhead x 12mm |
| 2 | Extrusion E2020 x 300mm |
| 2 | Extrusion E2040 x 150mm |
| 2 | Nut M3 hammer |

### 3D Printed parts

| 1 x Printbed_Strain_Relief.stl |
|----------|
| Printbed_Strain_Relief.stl |

### Sub-assemblies

| 1 x Z_Carriage_Center_assembly |
|----------|
| Z_Carriage_Center_assembled |

### Assembly instructions

Printbed_Frame_assembly

1. Slide the **Z_Carriage_Center_assembly** to the approximate center of the first 2040 extrusion and loosely tighten
the bolts. The bolts will be fully tightened when the Z_Carriage is aligned.
2. Bolt the **Printbed_Strain_Relief** to the second extrusion.
3. Slide the 2040 extrusion into the 2020 extrusions and loosely tighten the bolts. The bolts will be fully tightened after
the Z carriages are added.

Printbed_Frame_assembled

<span></span>
[Top](#TOP)

---

## Printbed_Frame_with_Z_Carriages assembly

### Sub-assemblies

| 1 x Printbed_Frame_assembly | 2 x Z_Carriage_Side_assembly |
|---|---|
| Printbed_Frame_assembled | Z_Carriage_Side_assembled |

### Assembly instructions

Printbed_Frame_with_Z_Carriages_assembly

1. Lay the frame on a flat surface and  slide the Z carriages onto the frame as shown.
2. Ensure the Z carriages are square and aligned with the end of the frame and then tighten the bolts on Z_carriages.
3. Ensure the 2040 extrusion is pressed firmly against the Z_Carriages and tighten the hidden bolts in the frame.

Printbed_Frame_with_Z_Carriages_assembled

<span></span>
[Top](#TOP)

---

## Printbed assembly

### Vitamins

| Qty | Description |
|----:|:---|
| 2 | Bolt M3 buttonhead x 10mm |
| 4 | Bolt M4 countersunk x 45mm |
| 1 | Heated Bed 235mm x 235mm |
| 4 | Heated bed leveling knob |
| 4 | Spring 8mm OD, 0.9mm gauge x 20mm long, closed end |

### 3D Printed parts

| 1 x Printbed_Strain_Relief_Clamp.stl |
|----------|
| Printbed_Strain_Relief_Clamp.stl |

### Sub-assemblies

| 1 x Printbed_Frame_with_Z_Carriages_assembly |
|----------|
| Printbed_Frame_with_Z_Carriages_assembled |

### Assembly instructions

Printbed_assembly

1. Attach the heated bed to the frame using the stacks of washers and O-rings as shown.
2. Spiral wrap the wires from the heated bed.
3. Use the **Printbed_Strain_Relief_Clamp** to clamp the wires to the frame.

Printbed_assembled

<span></span>
[Top](#TOP)

---

## Left_Side assembly

### Vitamins

| Qty | Description |
|----:|:---|
| 4 | Bolt M4 buttonhead x 10mm |
| 8 | Bolt M4 countersunk x 10mm |
| 8 | Bolt M5 buttonhead x 12mm |
| 2 | Extrusion E2020 x 400mm |
| 2 | Extrusion E2040 x 350mm |
|  12 | Nut M4 sliding T |
| 4 | SK12 shaft support bracket |

### 3D Printed parts

| 1 x Z_Motor_Mount.stl | 1 x Z_Motor_MountGuide_61mm.stl | 2 x Z_RodMountGuide_40mm.stl |
|---|---|---|
| Z_Motor_Mount.stl | Z_Motor_MountGuide_61mm.stl | Z_RodMountGuide_40mm.stl |

### Assembly instructions

Left_Side_assembly

1. Attach the SK brackets to the upper extrusion, use the **Z_RodMountGuide** to align the left bracket.
2. Tighten the bolts for the left bracket. Leave the bolts to the right bracket loosely tightened for now.
3. Attach the SK brackets and the **Z_Motor_Mount** to the lower extrusion, use the **Z_RodMountGuide** to
align the left bracket and the **Z_Motor_MountGuide** to align the motor mount. The motor itself will be added at a later
stage of the assembly.
4. Tighten the bolts for the left bracket and the **Z_Motor_Mount**. Leave the bolts to the right bracket loosely
tightened for now.
5. On a flat surface, bolt the upper and lower extrusions into the left and right uprights as shown. Tighten the bolts
continuously ensuring the frame is square.

Left_Side_assembled

<span></span>
[Top](#TOP)

---

## Left_Side_with_Printbed assembly

### Vitamins

| Qty | Description |
|----:|:---|
| 4 | Bolt M3 buttonhead x 10mm |
| 1 | Cork damper NEMA 17 |
| 2 | Linear rod 12mm x 300mm |
| 1 | Stepper motor NEMA17 x 40mm, 280mm integrated leadscrew |
| 1 | Stepper motor cable, 850mm |

### Sub-assemblies

| 1 x Left_Side_assembly | 1 x Printbed_assembly |
|---|---|
| Left_Side_assembled | Printbed_assembled |

### Assembly instructions

Left_Side_with_Printbed_assembly

1. Face the left face on a flat surface.
2. Attach the print bed to the left face by sliding the linear rods through the Z_Carriages.
3. Tighten the grub screws on the rod brackets, but don't yet tighten the bolts holding the brackets to the frame.
4. Slide the print bed to the top of the rods, and tighten the bolts in the top right rod bracket.
(you will have tightened the bolts on the top left bracket in a previous step).
5. Slide the print bed to the bottom of the rods and tighten the bolts on the bottom right rod bracket
(you will have tightened the bolts on the bottom left bracket in a previous step).
6. Thread the motor's lead screw through the lead nut on the **Z_Carriage_Center** and loosely bolt the motor to
the **Z_Motor_Mount**.
7. Ensure the **Z_Carriage_Center** is aligned with the lead screw and tighten the bolts on the **Z_Carriage_Center**
and the **Z_Motor_Mount**. The bolt holes on the **Z_Motor_Mount** are oval to allow some adjustment.
8. Route the motor wire through the lower extrusion channel and use the **E20_ChannelCover_50mm**s to hold it in place.

Left_Side_with_Printbed_assembled

<span></span>
[Top](#TOP)

---

## Stage_1 assembly

### Sub-assemblies

| 1 x Base_Plate_assembly | 1 x Left_Side_with_Printbed_assembly |
|---|---|
| Base_Plate_assembled | Left_Side_with_Printbed_assembled |

### Assembly instructions

Stage_1_assembly

1. Slide the left face into the base plate assembly.
2. Ensuring the frame remains square, tighten the hidden bolts and the bolts under the baseplate.

Stage_1_assembled

<span></span>
[Top](#TOP)

---

## Stage_2 assembly

### Sub-assemblies

| 1 x Right_Side_assembly | 1 x Stage_1_assembly |
|---|---|
| Right_Side_assembled | Stage_1_assembled |

### Assembly instructions

Stage_2_assembly

1. Slide the right face into the base plate assembly.
2. Ensuring the frame remains square, tighten the hidden bolts and the bolts under the baseplate.
3. Route the serial cable for the display in the top channel of the right side lower extrusion and route
the ribbon cable along the bottom of the extrusion and cover with the **E20_RibbonCover_50mm**s to keep
the cables in place.

Stage_2_assembled

<span></span>
[Top](#TOP)

---

## Stage_3 assembly

### Vitamins

| Qty | Description |
|----:|:---|
|  14 | Bolt M4 buttonhead x  8mm |
|  14 | Nut M4 hammer |
| 1 | Sheet polycarbonate 390mm x 400mm x 3mm |

### CNC Routed parts

| 1 x Back_Panel.dxf |
|----------|
| Back_Panel.dxf |

### Sub-assemblies

| 1 x Face_Top_assembly | 1 x Stage_2_assembly |
|---|---|
| Face_Top_assembled | Stage_2_assembled |

### Assembly instructions

Stage_3_assembly

1. Slide the **Face_Top** assembly into the rest of the frame and tighten the hidden bolts.
2. Check that the print head slides freely on the Y-axis. If it doesn't, then re-rack the Y-axis,
see [Face_Top_Stage_2 assembly](#Face_Top_Stage_2_assembly).
3. Attach the back panel to the rest of the assembly.
4. Tighten the bolts on the back panel.

Stage_3_assembled

<span></span>
[Top](#TOP)

---

## Stage_4 assembly

### Vitamins

| Qty | Description |
|----:|:---|
| 2 | Bolt M3 buttonhead x 10mm |
| 4 | Bolt M3 countersunk x 40mm |
| 1 | PTFE Bowden tube, 600 mm |

### 3D Printed parts

| 1 x Wiring_Guide.stl | 1 x Wiring_Guide_Clamp.stl |
|---|---|
| Wiring_Guide.stl | Wiring_Guide_Clamp.stl |

### Sub-assemblies

| 1 x Printhead_E3DV6_assembly | 1 x Stage_3_assembly |
|---|---|
| Printhead_E3DV6_assembled | Stage_3_assembled |

### Assembly instructions

Stage_4_assembly

1. Bolt the **Printhead_E3DV6_assembly** to the MGN carriage.
2. Route the wiring from the print head to the mainboard and secure it with the **Wiring_Guide_Clamp**.
3. Adjust the belt tension.
4. Connect the Bowden tube between the extruder and the printhead.

Stage_4_assembled

<span></span>
[Top](#TOP)

---

## main assembly

### Vitamins

| Qty | Description |
|----:|:---|
|  28 | Bolt M4 buttonhead x  8mm |
| 2 | Bolt M4 buttonhead x 12mm |
|  30 | Nut M4 hammer |
| 1 | Sheet polycarbonate 295mm x 400mm x 3mm |
| 1 | Sheet polycarbonate 390mm x 400mm x 3mm |

### 3D Printed parts

| 1 x Spool_Holder.stl | 1 x Spool_Holder_36.stl | 1 x Spool_Holder_Bracket.stl |
|---|---|---|
| Spool_Holder.stl | Spool_Holder_36.stl | Spool_Holder_Bracket.stl |

### CNC Routed parts

| 1 x Left_Side_Panel.dxf | 1 x Right_Side_Panel.dxf |
|---|---|
| Left_Side_Panel.dxf | Right_Side_Panel.dxf |

### Sub-assemblies

| 1 x Stage_4_assembly |
|----------|
| Stage_4_assembled |

### Assembly instructions

main_assembly

1. Bolt the polycarbonate sheet to the left face.
2. Attach the spoolholder and filament spool to the right face.
3. You are now ready to level the bed and calibrate the printer.

main_assembled

<span></span>
[Top](#TOP)

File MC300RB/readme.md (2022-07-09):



# MaybeCube Assembly Instructions

These are the assembly instructions for the MaybeCube. These instructions are not fully comprehensive, that is they do
not show every small detail of the construction and in particular they do not show the wiring. However there is
sufficient detail that someone with a good understanding of 3D printers can build the MaybeCube.

Main Assembly

## Read this before you order parts

2020, 2040 etc aluminium comes in variants with differing sized center holes - some are suitable for tapping for an
an M5 bolt and some are suitable for tapping for an M6 bolt. It doesn't really matter which you use, but ensure you
buy the bolts that correspond to your extrusion size. These build instructions assume M5 bolts, if your extrusion
requires M6 bolts then the 10mm and 12mm buttonhead M5 bolts should be replaced with M6 bolts.

The motor for the Z-axis has an integrated lead screw: in the *Parts List* the length specified is the length that
protrudes from the motor. Some suppliers specify the total length of the lead screw, that is including the part that
is inside the motor, so check how your supplier specifies the part before ordering. Another option is to order a lead
screw that is too long and cut to size, not however that lead screws are made from hardened steel and cannot be cut
with a hacksaw - an angle grinder is required to cut them.

This is a full build, some parts can be omitted to save cost, in particular:

* the Raspberry Pi camera (and corresponding 8mm M2 caphead bolts)
* the Raspberry Pi (if you don't want to run Octoprint or Klipper) and corresponding buck converter
* the Big Tree Tech relay module, if you don't want auto shut off
* the Big Tree Tech TFT display, if you are running Octoprint or Klipper
* I've specified a Big Tree Tech mainboard and display, you of course can use any mainboard and display you like
* the filament sensor
* the polycarbonate side and back panels, if you don't want to enclose your print volume for (say) printing ABS. Note
that these also add rigidity to the printer.

I've specified buttonhead bolts for the side and back panels. For a neater look you could countersink the holes and
use countersunk bolts.

## Printing the parts

A number of parts are in proximity with heat sources, namely the hotend, the heated bed and the motors. Ideally these
should be printed in ABS, but I have used PETG successfully. These parts are insulated from direct contact with the heat
sources, by cork underlay (for the heated bed) and by cork dampers (for the motors). These insulators should not be
omitted from the build.

<span></span>

---

## Table of Contents

1. [Parts list](#Parts_list)
1. [Printhead_E3DV6 assembly](#Printhead_E3DV6_assembly)
1. [X_Carriage_Belt_Side assembly](#X_Carriage_Belt_Side_assembly)
1. [XY_Motor_Mount_Right assembly](#XY_Motor_Mount_Right_assembly)
1. [XY_Motor_Mount_Left assembly](#XY_Motor_Mount_Left_assembly)
1. [XY_Idler_Right assembly](#XY_Idler_Right_assembly)
1. [XY_Idler_Left assembly](#XY_Idler_Left_assembly)
1. [Y_Carriage_Right assembly](#Y_Carriage_Right_assembly)
1. [Right_Side_Upper_Extrusion assembly](#Right_Side_Upper_Extrusion_assembly)
1. [Y_Carriage_Left assembly](#Y_Carriage_Left_assembly)
1. [Left_Side_Upper_Extrusion assembly](#Left_Side_Upper_Extrusion_assembly)
1. [Face_Top_Stage_1 assembly](#Face_Top_Stage_1_assembly)
1. [Face_Top_Stage_2 assembly](#Face_Top_Stage_2_assembly)
1. [Face_Top assembly](#Face_Top_assembly)
1. [Extruder_Bracket assembly](#Extruder_Bracket_assembly)
1. [Right_Side assembly](#Right_Side_assembly)
1. [Display_Cover_TFT35_E3 assembly](#Display_Cover_TFT35_E3_assembly)
1. [IEC_Housing assembly](#IEC_Housing_assembly)
1. [Base_Plate_Stage_1 assembly](#Base_Plate_Stage_1_assembly)
1. [Base_Plate assembly](#Base_Plate_assembly)
1. [Heated_Bed assembly](#Heated_Bed_assembly)
1. [Z_Carriage_Side assembly](#Z_Carriage_Side_assembly)
1. [Z_Carriage_Center assembly](#Z_Carriage_Center_assembly)
1. [Printbed_Frame assembly](#Printbed_Frame_assembly)
1. [Printbed_Frame_with_Z_Carriages assembly](#Printbed_Frame_with_Z_Carriages_assembly)
1. [Printbed assembly](#Printbed_assembly)
1. [Left_Side assembly](#Left_Side_assembly)
1. [Left_Side_with_Printbed assembly](#Left_Side_with_Printbed_assembly)
1. [Stage_1 assembly](#Stage_1_assembly)
1. [Stage_2 assembly](#Stage_2_assembly)
1. [Stage_3 assembly](#Stage_3_assembly)
1. [Stage_4 assembly](#Stage_4_assembly)
1. [Main assembly](#main_assembly)

<span></span>
[Top](#TOP)

---

## Parts list

| <span style="writing-mode: vertical-rl; text-orientation: mixed;">Printhead E3DV6</span> | <span style="writing-mode: vertical-rl; text-orientation: mixed;">X Carriage Belt Side</span> | <span style="writing-mode: vertical-rl; text-orientation: mixed;">Face Top</span> | <span style="writing-mode: vertical-rl; text-orientation: mixed;">Right Side</span> | <span style="writing-mode: vertical-rl; text-orientation: mixed;">Heated Bed</span> | <span style="writing-mode: vertical-rl; text-orientation: mixed;">Printbed</span> | <span style="writing-mode: vertical-rl; text-orientation: mixed;">Left Side</span> | <span style="writing-mode: vertical-rl; text-orientation: mixed;">Main</span> | <span style="writing-mode: vertical-rl; text-orientation: mixed;">TOTALS</span> |  |
|-----:|-----:|-----:|-----:|-----:|-----:|-----:|-----:|---:|:---|
| | | | | | | | | | **Vitamins** |
| .  | .  | .  | .  | .  | .  | .  | 1  | 1  |  Aluminium sheet 340mm x 340mm x 3mm |
| .  | .  |  24  | .  | .  | .  | .  | .  | 24  |  Ball bearing F623-2RS 3mm x 10mm x 4mm |
| .  | .  | 1  | .  | .  | .  | .  | .  | 1  |  Belt GT2 x 6mm x 1276mm |
| .  | .  | 1  | .  | .  | .  | .  | .  | 1  |  Belt GT2 x 6mm x 1300mm |
| .  | .  | .  | .  | .  | .  | .  | 1  | 1  |  BigTreeTech Relay Module v1.2 |
| .  | .  | .  | .  | .  | .  | .  | 1  | 1  |  BigTreeTech SKR v1.4 Turbo |
| .  | .  | .  | .  | .  | .  | .  | 1  | 1  |  BigTreeTech TFT35 E3 v3.0 |
| 4  | .  | .  | .  | .  | .  | .  | .  | 4  |  Bolt M2 caphead x  6mm |
| .  | .  | 4  | .  | .  | .  | .  | .  | 4  |  Bolt M2 caphead x  8mm |
| .  | .  |  14  | 2  | .  | 2  | .  |  20  | 38  |  Bolt M3 buttonhead x 10mm |
| .  | .  | .  | .  | .  | .  | .  |  18  | 18  |  Bolt M3 caphead x  6mm |
| .  | .  |  32  | .  | .  | 4  | .  | .  | 36  |  Bolt M3 caphead x 10mm |
| .  | .  | .  | .  | .  | .  | .  | 2  | 2  |  Bolt M3 caphead x 12mm |
| .  | .  | 2  | 2  | .  | .  | .  | .  | 4  |  Bolt M3 caphead x 16mm |
| .  | .  | .  | .  | 3  | .  | .  | .  | 3  |  Bolt M3 caphead x 20mm |
| .  | .  | 3  | .  | .  | .  | .  | 4  | 7  |  Bolt M3 caphead x 25mm |
| .  | .  | 1  | .  | .  | .  | .  | .  | 1  |  Bolt M3 caphead x 35mm |
| .  | 2  | .  | .  | .  | .  | .  | .  | 2  |  Bolt M3 caphead x 40mm |
| .  | .  | 2  | .  | .  | 2  | .  | 2  | 6  |  Bolt M3 countersunk x 10mm |
| .  | .  | 4  | .  | .  | .  | .  | 2  | 6  |  Bolt M3 countersunk x 12mm |
| 2  | .  | .  | .  | .  | .  | .  | .  | 2  |  Bolt M3 countersunk x 25mm |
| .  | .  | 4  | .  | .  | .  | .  | .  | 4  |  Bolt M3 countersunk x 35mm |
| .  | .  | .  | .  | .  | .  | .  | 4  | 4  |  Bolt M3 countersunk x 40mm |
| .  | .  | .  | 8  | .  | .  | .  |  55  | 63  |  Bolt M4 buttonhead x  8mm |
| .  | .  |  12  | .  | .  | 6  | 4  |  14  | 36  |  Bolt M4 buttonhead x 10mm |
| .  | .  | 8  | .  | .  | .  | .  | 4  | 12  |  Bolt M4 buttonhead x 12mm |
| .  | .  |  20  | .  | .  | .  | 8  | .  | 28  |  Bolt M4 countersunk x 10mm |
| .  | .  | 6  | .  | .  | .  | .  | .  | 6  |  Bolt M5 buttonhead x 10mm |
| .  | .  |  10  | 8  | .  | 8  | 8  |  14  | 48  |  Bolt M5 buttonhead x 12mm |
| .  | .  | .  | .  | .  | 4  | .  | .  | 4  |  Bolt M5 buttonhead x 16mm |
| .  | .  | .  | .  | .  | 4  | .  | .  | 4  |  Bolt M5 countersunk x 12mm |
| .  | .  | 2  | 1  | .  | .  | .  | 1  | 4  |  Cork damper NEMA 17 |
| .  | .  | .  | .  | .  | 1  | .  | .  | 1  |  Cork underlay 214mm x 214mm |
| .  | .  | .  | .  | .  | 2  | .  | .  | 2  |  Extrusion E2020 x 265mm |
| .  | .  | .  | .  | .  | .  | .  | 1  | 1  |  Extrusion E2020 x 300mm |
| .  | .  | .  | 2  | .  | .  | 2  | .  | 4  |  Extrusion E2020 x 400mm |
| .  | .  | .  | .  | .  | 2  | .  | .  | 2  |  Extrusion E2040 x 188mm |
| .  | .  | 4  | 2  | .  | .  | 2  | 1  | 9  |  Extrusion E2040 x 300mm |
| .  | .  | .  | .  | .  | .  | .  | 1  | 1  |  Extrusion E2080 x 300mm |
| 1  | .  | .  | .  | .  | .  | .  | .  | 1  |  Fan 30mm x 10mm |
| .  | .  | .  | 1  | .  | .  | .  | .  | 1  |  Filament sensor |
| .  | .  | .  | .  | 1  | .  | .  | .  | 1  |  Heated Bed 214mm x 214mm |
| .  | .  | 4  | .  | .  | .  | .  | .  | 4  |  Heatfit insert M3 |
| 1  | .  | .  | .  | .  | .  | .  | .  | 1  |  Hot end E3D V6 direct 1.75mm |
| .  | .  | .  | .  | .  | .  | .  | 1  | 1  |  IEC320 C14 switched fused inlet module |
| .  | .  | .  | .  | .  | 1  | .  | .  | 1  |  Leadscrew nut 8 x 2 |
| .  | .  | 1  | .  | .  | .  | .  | .  | 1  |  Linear rail MGN12 x 250mm |
| .  | .  | 2  | .  | .  | .  | .  | .  | 2  |  Linear rail MGN12 x 300mm |
| .  | .  | 3  | .  | .  | .  | .  | .  | 3  |  Linear rail carriage MGN12H |
| .  | .  | .  | .  | .  | .  | .  | 2  | 2  |  Linear rod 12mm x 300mm |
| .  | .  | .  | 1  | .  | .  | .  | .  | 1  |  MK10 Dual Pulley Extruder |
| .  | .  | .  | .  | .  | .  | .  | 1  | 1  |  Micro SD card |
| .  | .  |  20  | .  | 3  | 2  | .  | 6  | 31  |  Nut M3 hammer |
| .  | .  |  12  | 8  | .  | .  | .  |  69  | 89  |  Nut M4 hammer |
| .  | .  |  36  | .  | .  | 6  |  12  | .  | 54  |  Nut M4 sliding T |
| .  | .  | .  | .  |  12  | .  | .  | .  | 12  |  O-ring nitrile 4mm x 2mm |
| .  | .  | .  | .  | .  | .  | .  | 1  | 1  |  PSU NIUGUY CB-500W-24V |
| .  | .  | .  | .  | .  | .  | .  | 1  | 1  |  PTFE Bowden tube, 500 mm |
| .  | .  | .  | .  | .  | .  | .  |  12  | 12  |  Pillar hex nylon F/F M3x10 |
| .  | .  | .  | 2  | .  | .  | .  | .  | 2  |  Pillar hex nylon F/F M3x14 |
| .  | .  | .  | .  | .  | .  | .  | 2  | 2  |  Pillar hex nylon F/F M3x25 |
| .  | .  | .  | .  | .  | .  | .  | 2  | 2  |  Pillar hex nylon F/F M3x5 |
| .  | .  | 2  | .  | .  | .  | .  | .  | 2  |  Pulley GT2OB 20 teeth |
| .  | .  | .  | .  | .  | .  | .  | 1  | 1  |  Raspberry Pi 3A+ |
| .  | .  | 1  | .  | .  | .  | .  | .  | 1  |  Raspberry Pi camera V2 |
| .  | .  | .  | .  | .  | 2  | .  | .  | 2  |  SCS12LUU bearing block |
| .  | .  | .  | .  | .  | .  | 4  | .  | 4  |  SK12 shaft support bracket |
| .  | .  | .  | .  | .  | .  | .  | 1  | 1  |  Sheet polycarbonate 245mm x 400mm x 3mm |
| .  | .  | .  | .  | .  | .  | .  | 2  | 2  |  Sheet polycarbonate 340mm x 400mm x 3mm |
| 1  | .  | .  | .  | .  | .  | .  | .  | 1  |  Square radial fan 3010 |
| .  | .  | .  | .  | .  | .  | .  | 1  | 1  |  Stepper motor NEMA17 x 40mm, 280mm integrated leadscrew |
| .  | .  | 2  | 1  | .  | .  | .  | .  | 3  |  Stepper motor NEMA17 x 47mm |
| .  | .  | .  | 1  | .  | .  | .  | .  | 1  |  Stepper motor cable, 200mm |
| .  | .  | 1  | .  | .  | .  | .  | .  | 1  |  Stepper motor cable, 300mm |
| .  | .  | 1  | .  | .  | .  | .  | .  | 1  |  Stepper motor cable, 500mm |
| .  | .  | .  | .  | .  | .  | .  | 1  | 1  |  Stepper motor cable, 750mm |
| .  | 2  |  38  | .  |  12  | .  | .  | .  | 52  |  Washer M3 |
| .  | .  | .  | .  | 3  | .  | .  | .  | 3  |  Washer penny M4 |
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

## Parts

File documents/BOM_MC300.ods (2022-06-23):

Total Cost
Item | Quantity | Optional | Price | Cost | Optional Cost | Weight/g | Acc Weight/9 | Notes
Total Cost |  |  |  | £431.67 |  |  | 3.45
Motion system XY
Stepper motor NEMA17 x 40mm | 2 |  | £9.40 | £18.80 |  |  | 0
Cork damper NEMA 17 | 2 |  | £0.27 | £0.54 |  |  | 0
Stepper motor cable, 300mm | 1 |  | £0.00 | £0.00 |  |  | 0 | included with stepper motor
Stepper motor cable, 500mm | 1 |  | £0.00 | £0.00 |  |  | 0 | included with stepper motor
Pulley GT2OB 20 teeth | 2 |  | £0.40 | £0.80 |  |  | 0
Pulley GT2 idler 16 teeth | 8 |  | £0.40 | £3.20 |  |  | 0
Pulley GT2 idler smooth 9.63mm | 4 |  | £0.40 | £1.60 |  |  | 0
Linear rail MGN12 x 250mm | 1 |  | £9.63 | £9.63 |  | 165 | 165
Linear rail MGN12 x 300mm | 2 |  | £9.99 | £19.98 |  | 198 | 396
Linear rail carriage MGN12H | 3 |  | £0.00 | £0.00 |  | 50 | 150 | included with linear rails
Belt GT2 x 6mm, 3 meters | 1 |  | £6.10 | £6.10 |  |  | 0
Motion system Z
Stepper motor NEMA17 x 40mm, 280mm integrated leadscrew | 1 |  | £23.10 | £23.10 |  |  | 0
Leadscrew nut 8 x 2 | 1 |  | £0.00 | £0.00 |  |  | 0 | included with stepper motor
Stepper motor cable, 750mm | 1 |  | £0.00 | £0.00 |  |  | 0 | included with stepper motor
Cork damper NEMA 17 | 1 |  | £0.27 | £0.27 |  |  | 0
Linear rod 12mm x 300mm | 2 |  | £5.41 | £10.82 |  |  | 0
SK12 shaft support bracket | 4 |  | £1.14 | £4.56 |  |  | 0
SCS12LUU bearing block | 2 |  | £4.42 | £8.84 |  |  | 0
Extruder
MK10 Dual Pulley Extruder | 1 |  | £6.56 | £6.56 |  |  | 0
Stepper motor NEMA17 x 47mm | 1 |  | £9.99 | £9.99 |  |  | 0
Stepper motor cable, 200mm | 1 |  | £0.00 | £0.00 |  |  | 0 | included with stepper motor
Cork damper NEMA 17 | 1 |  | £0.27 | £0.27 |  |  | 0
Filament sensor |  | 1
Hot end
E3D v6 Hotend Full Kit | 1 |  | 52.80 | £52.80 |  |  | 0 | includes everything for hotend except radial fan
Hot end E3D V6 direct 1.75mm | 1 |  |  |  |  |  | 0 | included in kit
50W Cartridge heater |  |  |  |  |  |  | 0
Thermistor sensor cartridge |  |  |  |  |  |  | 0
Fan 30mm x 10mm |  |  |  |  |  |  | 0
E3D V6 Fan Duct |  |  |  |  |  |  | 0
Hot end fixings kit |  |  |  |  |  |  | 0
PTFE tube 500 mm |  |  |  |  |  |  | 0
Silicone sock |  |  |  |  |  |  | 0
Square radial fan 3010 | 1 |  | £5.99 | £5.99 |  |  | 0
Printbed
Heated Bed 214mm x 214mm | 1 |  | £15.40 | £15.40 |  |  | 0
Cork underlay 214mm x 214mm | 1 |  | £3.00 | £3.00 |  |  | 0
O-ring nitrile 4mm x 2mm | 9 |  | £0.30 | £2.70 |  |  | 0
Extrusion E2020 x 265mm | 2 |  | £3.00 | £6.00 |  |  | 0
Extrusion E2040 x 188mm | 2 |  | £3.00 | £6.00 |  |  | 0
Frame
Extrusion E2020 x 300mm | 1 |  | £3.00 | £3.00 |  | 136 | 136
Extrusion E2020 x 400mm | 4 |  | £4.00 | £16.00 |  | 180 | 720
Extrusion E2040 x 300mm | 8 |  | £3.50 | £28.00 |  | 235 | 1880
Extrusion E2080 x 300mm | 1 |  | £7.50 | £7.50 |  |  | 0
Aluminium sheet 340mm x 340mm x 3mm | 1 |  | £19.00 | £19.00 |  |  | 0
Polycarbonate sheet 250mm x 400mm x 3mm | 1 |  |  | £22.00 |  |  | 0 | cut from a 1000m x 500mm sheet
Polycarbonate sheet 340mm x 400mm x 3mm | 2 |  |  |  |  |  | 0
Electronics and related
MINI E3 V3.0 Control Board with TFT35 E3 V3.0 Screen 3 | 1 |  | £68.05 | £68.05 |  |  | 0
Micro SD card | 1 |  | £7.00 | £7.00 |  |  | 0
Pillar hex nylon F/F M3x20 | 4 |  | £0.04 | £0.16 |  |  | 0
LED Switching Power Supply 24V 15A 360W | 1 |  | £14.85 | £14.85 |  |  | 0
IEC320 C14 switched fused inlet module | 1 |  | £1.72 | £1.72 |  |  | 0
Raspberry Pi 3A+ |  | 1 | £23.40 | £0.00 |  |  | 0
Raspberry Pi camera V2 |  | 1 |  | £0.00 |  |  | 0
Pillar hex nylon F/F M3x10 |  | 4 | £0.04 | £0.00 |  |  | 0
Buck converter, 24V to 5V |  | 1 | £3.65 | £0.00 |  |  | 0
Pillar hex nylon F/F M3x14 |  | 2 | £0.04 | £0.00 |  |  | 0
Cable Management
Ziptie 2.5mm x 100mm min length | 3 |  | £0.04 | £0.12 |  |  | 0
Tools
Nuts and Bolts |  |  |  | £27.32
Heatfit insert M3 | 4 |  | £0.04 | £0.16 |  |  | 0
Bolt M2 caphead x 6mm | 4 |  | £0.01 | £0.04 |  |  | 0
Bolt M2 caphead x 8mm | 4 |  | £0.01 | £0.04 |  |  | 0
Bolt M3 caphead x 6mm | 12 |  | £0.01 | £0.12 |  |  | 0
Bolt M3 caphead x 10mm | 36 |  | £0.01 | £0.36 |  |  | 0
Bolt M3 caphead x 16mm | 2 |  | £0.01 | £0.02 |  |  | 0
Bolt M3 caphead x 20mm | 3 |  | £0.01 | £0.03 |  |  | 0
Bolt M3 caphead x 25mm | 6 |  | £0.01 | £0.06 |  |  | 0
Bolt M3 caphead x 30mm | 2 |  | £0.01 | £0.02 |  |  | 0
Bolt M3 caphead x 40mm | 2 |  | £0.01 | £0.02 |  |  | 0
Bolt M3 countersunk x 8mm | 2 |  | £0.01 | £0.02 |  |  | 0
Bolt M3 countersunk x 10mm | 4 |  | £0.01 | £0.04 |  |  | 0
Bolt M3 countersunk x 12mm | 4 |  | £0.01 | £0.04 |  |  | 0
Bolt M3 countersunk x 25mm | 10 |  | £0.01 | £0.10 |  |  | 0
Bolt M3 countersunk x 30mm | 4 |  | £0.01 | £0.04 |  |  | 0
Bolt M3 buttonhead x 10mm | 10 |  | £0.01 | £0.10 |  |  | 0
Bolt M3 buttonhead x 12mm | 16 |  | £0.01 | £0.16 |  |  | 0
Bolt M3 buttonhead x 16mm | 2 |  | £0.01 | £0.02 |  |  | 0
Bolt M3 buttonhead x 8mm | 4 |  | £0.01 | £0.04 |  |  | 0
Bolt M4 countersunk x 8mm | 21 |  | £0.08 | £1.68 |  |  | 0
Bolt M4 countersunk x 10mm | 28 |  | £0.08 | £2.24 |  |  | 0
Bolt M4 buttonhead x 8mm | 46 |  | £0.08 | £3.68 |  |  | 0
Bolt M4 buttonhead x 10mm | 38 |  | £0.08 | £3.04 |  |  | 0
Bolt M4 buttonhead x 12mm | 14 |  | £0.08 | £1.12 |  |  | 0
Bolt M5 countersunk x 12mm | 8 |  | £0.10 | £0.80 |  |  | 0
Bolt M5 buttonhead x 10mm | 4 |  | £0.10 | £0.40 |  |  | 0
Bolt M5 buttonhead x 12mm | 46 |  | £0.10 | £4.60 |  |  | 0
Nut M3 hammer | 24 |  | £0.04 | £0.96 |  |  | 0
Nut M3 sliding T | 3 |  | £0.08 | £0.24 |  |  | 0
Nut M4 hammer | 87 |  | £0.04 | £3.48 |  |  | 0
Nut M4 sliding T | 48 |  | £0.07 | £3.36 |  |  | 0
Washer M3 | 37 |  | £0.01 | £0.37 |  |  | 0
Washer penny M4 | 6 |  | £0.01 | £0.06 |  |  | 0
Washer M4 | 2 |  | £0.01 | £0.02 |  |  | 0

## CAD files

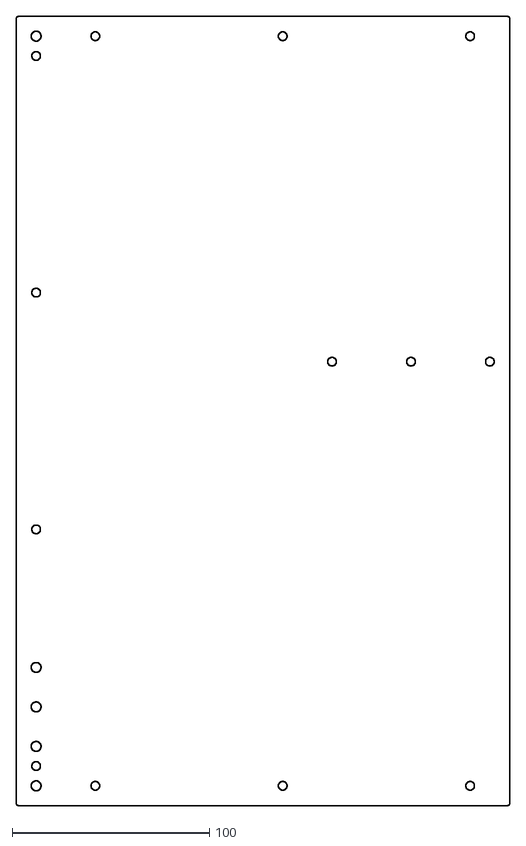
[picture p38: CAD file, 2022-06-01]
MC300/dxfs/Right_Side_Panel.dxf
250.0 x 400.0

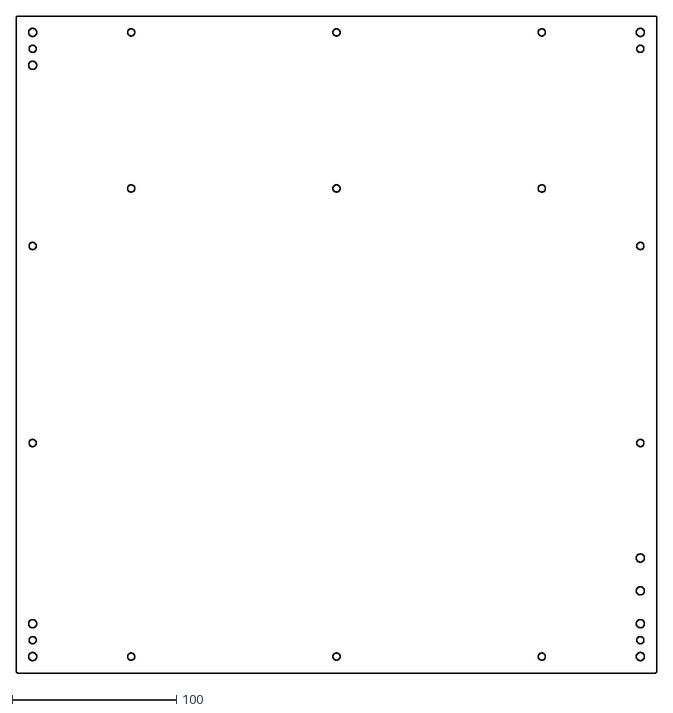
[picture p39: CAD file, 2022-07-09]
MC350/dxfs/Left_Side_Panel.dxf
390.0 x 400.0

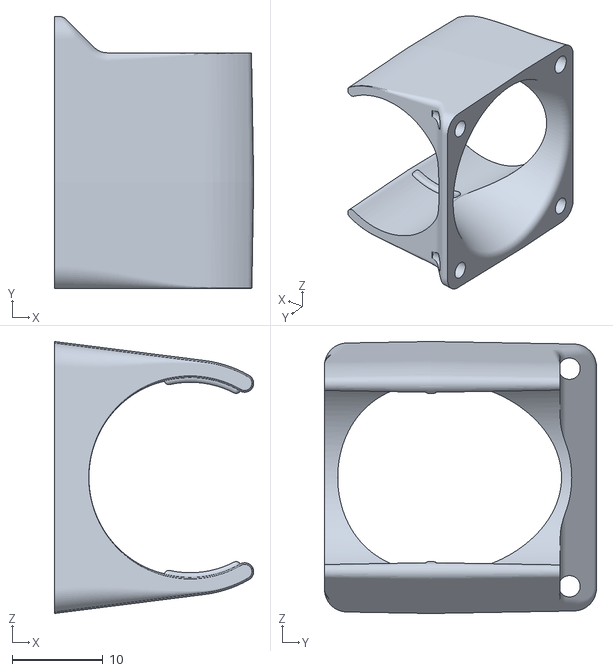
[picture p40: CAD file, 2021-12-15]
scad/stlimport/E3D_V6_6_Duct.stl
22.0 x 30.0 x 30.0

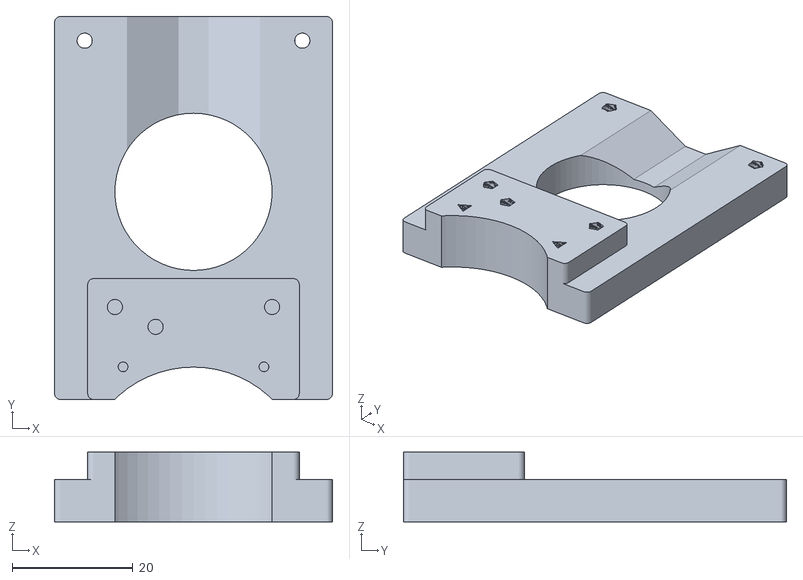
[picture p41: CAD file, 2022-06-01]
Voron_Mini_Afterburner/stls/X_Carriage_Voron_Mini_Afterburner.stl
46.0 x 63.4 x 11.5

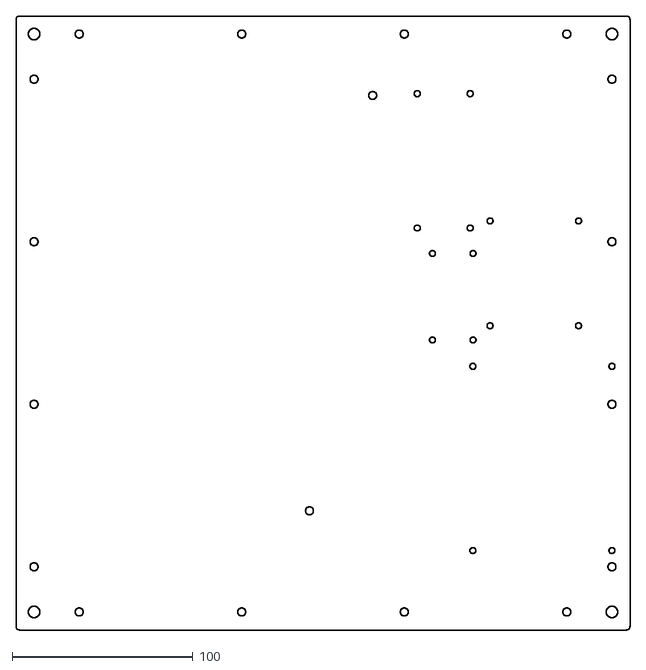
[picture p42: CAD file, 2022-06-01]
MC300/dxfs/BaseAL.dxf
340.0 x 340.0

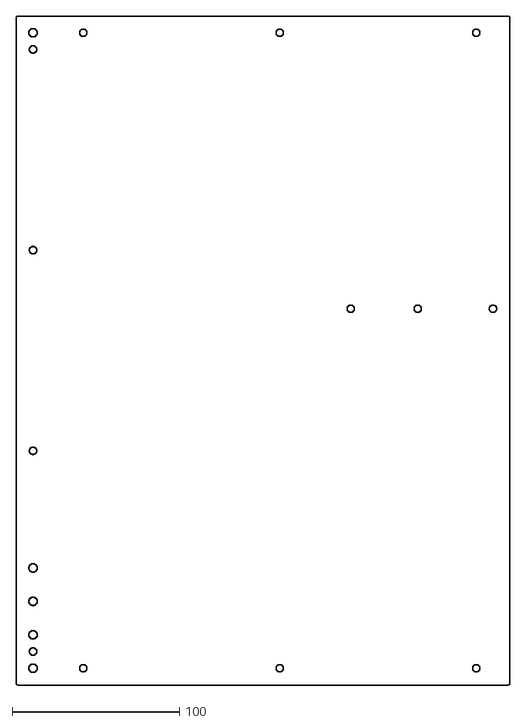
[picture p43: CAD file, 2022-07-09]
MC350/dxfs/Right_Side_Panel.dxf
295.0 x 400.0

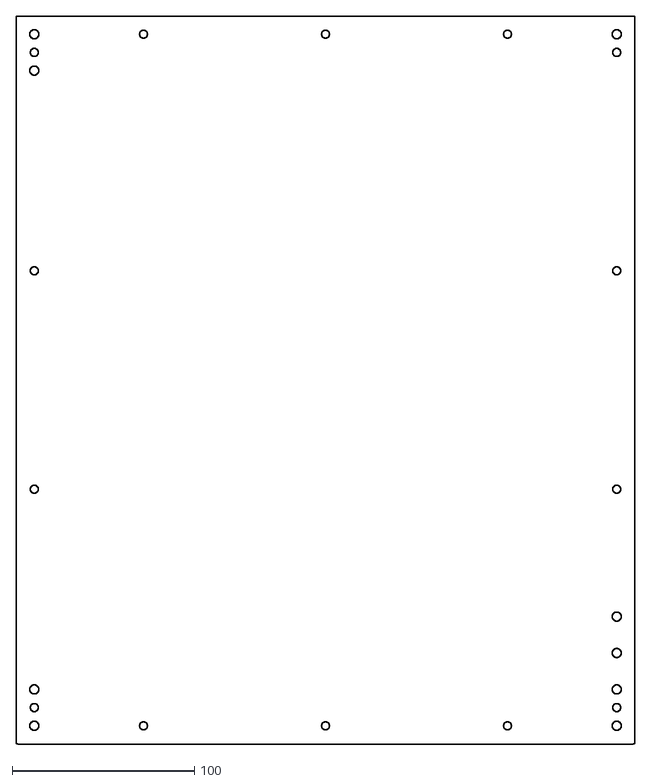
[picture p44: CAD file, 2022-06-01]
MC300/dxfs/Left_Side_Panel.dxf
340.0 x 400.0

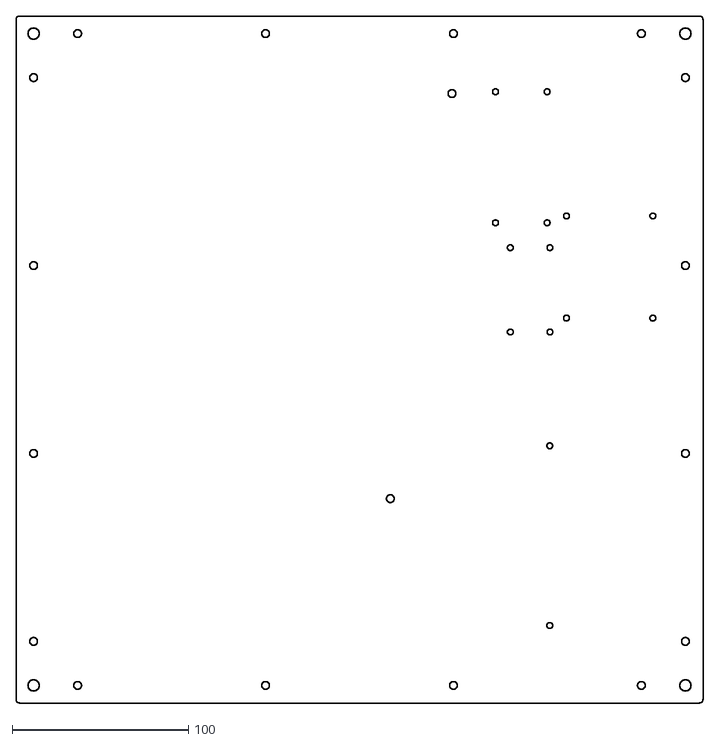
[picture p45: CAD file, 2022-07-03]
MC350/dxfs/BaseAL.dxf
390.0 x 390.0

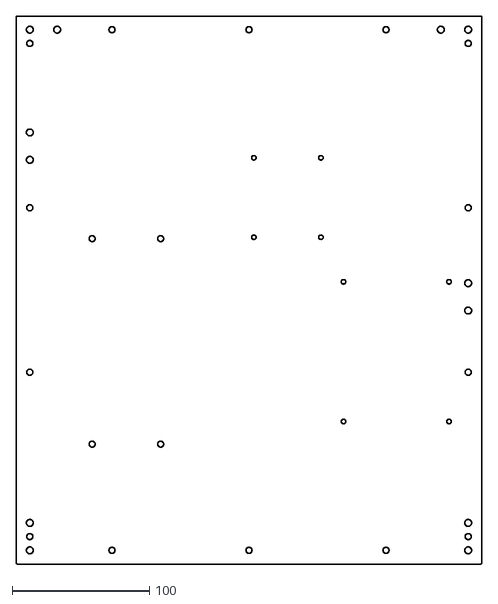
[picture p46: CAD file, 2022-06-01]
MC300/dxfs/Back_Panel.dxf
340.0 x 400.0

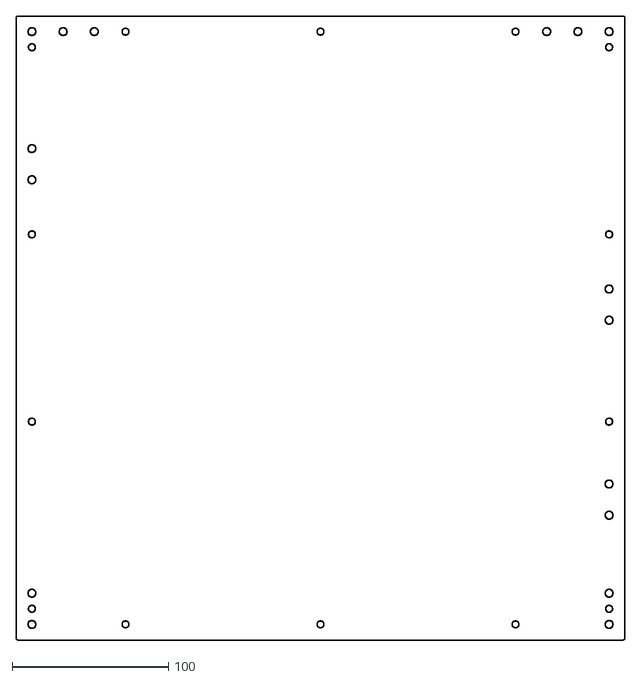
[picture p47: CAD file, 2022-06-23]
MC350/dxfs/Back_Panel.dxf
390.0 x 400.0

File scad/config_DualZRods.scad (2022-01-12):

_variant = "DualZRods";

__extrusionLengths = [350, 350, 400];
eX = __extrusionLengths.x;
eY = __extrusionLengths.y;
eZ = __extrusionLengths.z;

eSize = 20; // for 2020, 2040  etc extrusion

_xyMotorDescriptor = "NEMA17_48";
_zMotorDescriptor = "NEMA17_40L280";
_corkDamperThickness = 2;

_xRailLength = eX - 50;
_yRailLength = eY;
_zRodLength = eZ - 100;

_xCarriageDescriptor = "MGN12H";
_xCarriageCountersunk = true;
_yCarriageDescriptor = "MGN12H";


_coreXYDescriptor = "GT2_20_25";

_use2060ForTop = true;
_useDualZRods = true;
_useDualZMotors = false;
_useElectronicsInBase = true;
_useFrontDisplay = false;
_useSidePanels = false;

_printbedSize = [235, 235, 4]; // Ender 3 size
_printbedArmSeparation = 150;
_printbed4PointSupport = true;

_blowerDescriptor = "BL30x10";

// set this so the zRod brackets clear the xy motors
// limited by printbed frame hitting XY motors and possibly extruder motor
__skBracketWidth = 42; // same for SK8, SK10, and SK12
_zRodOffsetY = __skBracketWidth/2 + 40;
_zLeadScrewOffset = 23;// ensures clearance of zMotor from frame and alignment with zRods
_upperZRodMountsExtrusionOffsetZ = eZ - 95;

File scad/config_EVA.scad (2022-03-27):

_variant = "EVA";

__extrusionLengths = [350, 350, 400];
eX = __extrusionLengths.x;
eY = __extrusionLengths.y;
eZ = __extrusionLengths.z;

eSize = 20;

_xyMotorDescriptor = "NEMA17_48";

_xRailLength = eX - 50;
_yRailLength = eY;
_xCarriageDescriptor = "MGN12H";
_xCarriageCountersunk = true;
_yCarriageDescriptor = "MGN12H";

_useReversedBelts = false;

_coreXYDescriptor = "GT2_20_16";

__skBracketWidth = 42; // same for SK8, SK10, and SK12
_zRodOffsetY = __skBracketWidth/2 + 40;

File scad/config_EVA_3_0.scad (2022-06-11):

include <config_EVA_2_4_2.scad>

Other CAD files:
scad/config_EVA_2_4_2.scad
scad/BackFace.scad
scad/BasePlate.scad
scad/FaceLeft.scad
scad/FaceRight.scad
scad/FaceRightExtras.scad
scad/FaceTop.scad
scad/Main.scad
scad/MainAssemblies.scad
scad/MainAssemblyChannelNuts.scad
scad/MainAssemblyDualZRods.scad
scad/MainAssemblyEVA.scad
scad/MainAssemblyEVA_2_4_2.scad
scad/MainAssemblyEVA_3_0.scad
scad/MainAssemblyJigs.scad
scad/MainAssemblyJubileeToolChanger.scad
scad/MainAssemblyKinematicBed.scad
scad/MainAssemblyM5.scad
scad/MainAssemblyToolChanger.scad
scad/MainAssemblyVoronAfterburner.scad
scad/MainAssemblyVoronMiniAfterburner.scad
scad/MainAssemblyXChange.scad
scad/Parameters_CoreXY.scad
scad/Parameters_Main.scad
scad/Parameters_Positions.scad
scad/Printbed.scad
scad/config_JubileeKinematicBed.scad
scad/config_JubileeToolchanger.scad
scad/config_KinematicBed.scad
scad/config_M5.scad
scad/config_MC250.scad
scad/config_MC290.scad
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

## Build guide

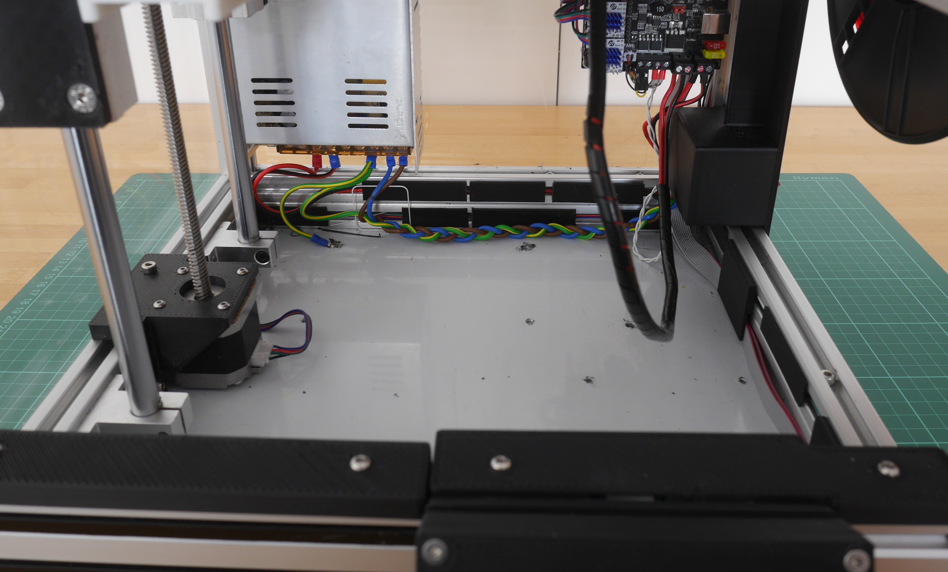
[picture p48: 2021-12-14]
pictures/MC_wiring.jpg

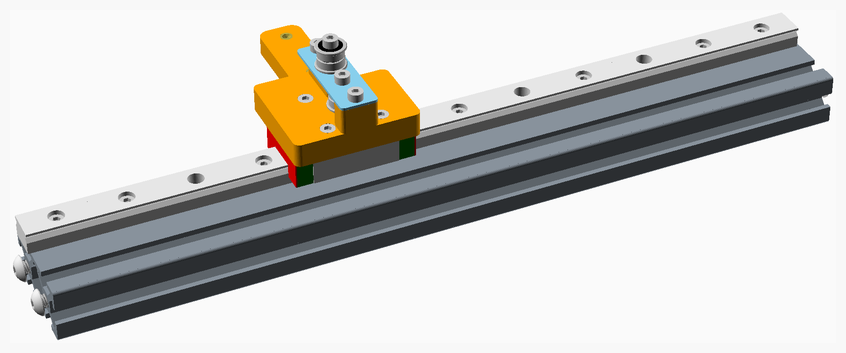
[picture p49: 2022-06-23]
MC300RB/assemblies/Left_Side_Upper_Extrusion_assembled.png

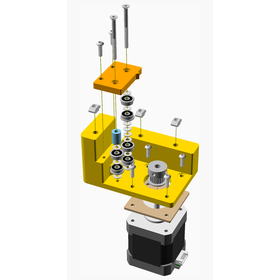
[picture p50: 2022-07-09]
MC350/assemblies/XY_Motor_Mount_Left_assembly_tn.png

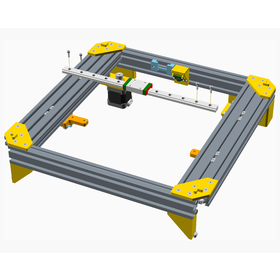
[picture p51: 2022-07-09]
MC350/assemblies/Face_Top_Stage_2_assembly_tn.png

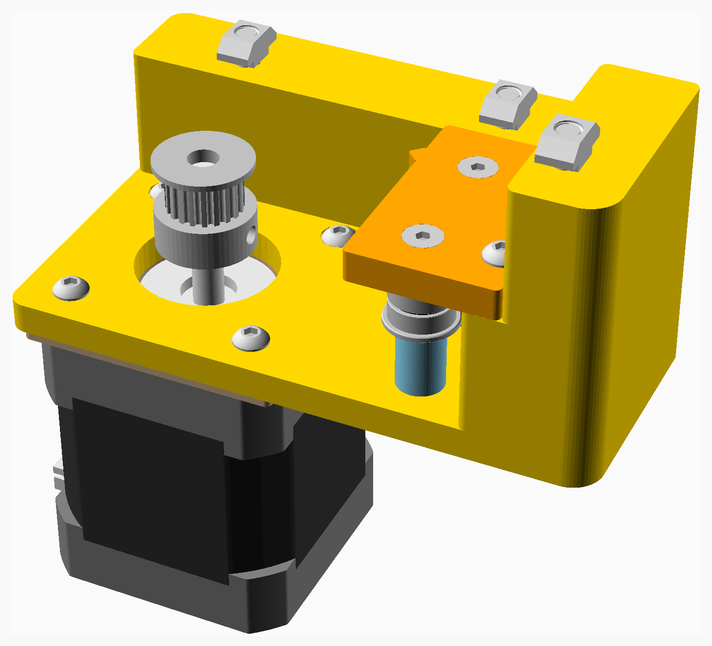
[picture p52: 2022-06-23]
MC300RB/assemblies/XY_Motor_Mount_Right_assembled.png

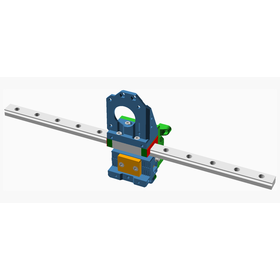
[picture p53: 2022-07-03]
EVA_2_4_2/assemblies/EVA_2_4_2_Stage_1_assembled_tn.png

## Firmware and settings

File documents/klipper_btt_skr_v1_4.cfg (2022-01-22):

# This file contains common pin mappings for the BIGTREETECH SKR V1.4
# board. To use this config, the firmware should be compiled for the
# LPC1768 or LPC1769(Turbo).

# See docs/Config_Reference.md for a description of parameters.

[mcu]
## Change to value obtained by "ls -l /dev/serial/by-id/"
serial: /dev/serial/by-id/usb-Klipper_Klipper_firmware_12345-if00

[printer]
kinematics: corexy
max_velocity: 300
max_accel: 5000
max_z_velocity: 25
max_z_accel: 30

########################################
#   X/Y/Z Stepper Settings
########################################

# Steppers are set with
# 1. No hold current, since changing motor current can induce motor movement
# 2. spreadCycle mode, so stealthchop_threshold not set
# 3. Interpolation disabled for best possible accuracy, so interpolate set to False

[stepper_x]
step_pin: P2.2
dir_pin: P2.6
enable_pin: !P2.1
microsteps: 16
# Marlin DEFAULT_AXIS_STEPS_PER_UNIT 80
# rotation_distance = <full_steps_per_rotation> * <microsteps> / <steps_per_mm>
# rotation_distance = 200 * 16 / 80;
rotation_distance: 40
endstop_pin: !P1.29
position_endstop: 0
position_max: 184
# sensorless homing, homing speed should be half rotation_distance
homing_speed: 20
homing_retract_dist: 0
endstop_pin: tmc2209_stepper_x:virtual_endstop

[tmc2209 stepper_x]
uart_pin: P1.10
run_current: 0.800
#hold_current: 0.500
interpolate: False
# sensorless homing
diag_pin: ^P1.29    # Set to MCU pin connected to TMC DIAG pin
driver_SGTHRS: 255   # 255 is most sensitive value, 0 is least sensitive

[stepper_y]
step_pin: P0.19
dir_pin: P0.20
enable_pin: !P2.8
microsteps: 16
# Marlin DEFAULT_AXIS_STEPS_PER_UNIT 80
# rotation_distance = <full_steps_per_rotation> * <microsteps> / <steps_per_mm>
# rotation_distance = 200 * 16 / 80;
rotation_distance: 40
endstop_pin: !P1.28
position_endstop: 0
position_max: 184
# sensorless homing, homing speed should be half rotation_distance
homing_speed: 20
homing_retract_dist: 0
endstop_pin: tmc2209_stepper_y:virtual_endstop

[tmc2209 stepper_y]
uart_pin: P1.9
run_current: 0.800
#hold_current: 0.500
interpolate: False
# sensorless homing
diag_pin: ^P1.28    # Set to MCU pin connected to TMC DIAG pin
driver_SGTHRS: 255   # 255 is most sensitive value, 0 is least sensitive

[stepper_z]
step_pin: P0.22
dir_pin: !P2.11
enable_pin: !P0.21
microsteps: 16
# Marlin DEFAULT_AXIS_STEPS_PER_UNIT 400
# rotation_distance = <full_steps_per_rotation> * <microsteps> / <steps_per_mm>
# rotation_distance = 200 * 16 / 400;
rotation_distance: 8
endstop_pin: !P1.27
position_endstop: 203
position_max: 203
# sensorless homing, homing speed should be half rotation_distance
homing_speed: 4
homing_retract_dist: 0
endstop_pin: tmc2209_stepper_z:virtual_endstop

[tmc2209 stepper_z]
uart_pin: P1.8
run_current: 0.650
#hold_current: 0.450
interpolate: False
# sensorless homing
diag_pin: ^P1.27    # Set to MCU pin connected to TMC DIAG pin
driver_SGTHRS: 255   # 255 is most sensitive value, 0 is least sensitive

########################################
#   Extruder
########################################

[extruder]
step_pin: P2.13
dir_pin: !P0.11
enable_pin: !P2.12
microsteps: 16
# Marlin DEFAULT_AXIS_STEPS_PER_UNIT 148
# rotation_distance = <full_steps_per_rotation> * <microsteps> / <steps_per_mm>
# rotation_distance = 200 * 16 / 148;
rotation_distance: 21.622
nozzle_diameter: 0.600
filament_diameter: 1.750
heater_pin: P2.7
sensor_type: EPCOS 100K B57560G104F
sensor_pin: P0.24
control: pid
pid_Kp: 15.77
pid_Ki: 1.02
pid_Kd: 60.68
min_temp: 0
max_temp: 260

[tmc2209 extruder]
uart_pin: P1.4
run_current: 0.800
#hold_current: 0.500
interpolate: False

########################################
#   Fan Control
########################################

[heater_fan hotend_fan]
# Hotend fan
pin: P2.4
kick_start_time: 0.500
heater: extruder
heater_temp: 50.0

[fan]
# Print cooling fan
pin: P2.3
kick_start_time: 0.500

########################################
#   Heated Bed
########################################

[heater_bed]
heater_pin: P2.5
sensor_type: EPCOS 100K B57560G104F
sensor_pin: P0.25
control: pid
pid_Kp: 60.7
pid_Ki: 9.93
pid_Kd: 247.41
min_temp: 0
max_temp: 130

########################################
#   Resonance measurement
########################################

# Must set up the RPi as a secondary MCU to do this, see: https://www.klipper3d.org/RPi_microcontroller.html

#[mcu rpi]
#serial: /tmp/klipper_host_mcu

#[adxl345]
#cs_pin: rpi:None

#[resonance_tester]
#accel_chip: adxl345
#probe_points:
#    90,90,20  # 20mm above mid point of bed

########################################
#   EXP1 / EXP2 (display) pins
########################################

[board_pins]
aliases:
    # EXP1 header
    EXP1_1=P1.30, EXP1_3=P1.18, EXP1_5=P1.20, EXP1_7=P1.22, EXP1_9=<GND>,
    EXP1_2=P0.28, EXP1_4=P1.19, EXP1_6=P1.21, EXP1_8=P1.23, EXP1_10=<5V>,
    # EXP2 header
    EXP2_1=P0.17, EXP2_3=P3.26, EXP2_5=P3.25, EXP2_7=P1.31, EXP2_9=<GND>,
    EXP2_2=P0.15, EXP2_4=P0.16, EXP2_6=P0.18, EXP2_8=<RST>, EXP2_10=<NC>
    # Pins EXP2_1, EXP2_6, EXP2_2 are also MISO, MOSI, SCK of bus "ssp0"


######################################################################
# "RepRapDiscount 128x64 Full Graphic Smart Controller" type displays
######################################################################

# In Marlin:
# #define REPRAP_DISCOUNT_FULL_GRAPHIC_SMART_CONTROLLER

[display]
lcd_type: st7920
cs_pin: EXP1_4
sclk_pin: EXP1_5
sid_pin: EXP1_3
encoder_pins: ^EXP2_3, ^EXP2_5
click_pin: ^!EXP1_2
#kill_pin: ^!EXP2_8

[output_pin beeper]
pin: EXP1_1

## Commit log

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2021-04-27 Fixed XY_Idler_Left_assembly title.
    [XY_Idler.scad]
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2021-04-27 Reverted to standard 16T idler for MC300.
    [config_MC300.scad]
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2021-04-28 Changed Face_ left and right to left and right _Side.
    [BackFace.scad, Base.scad, FaceLeft.scad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]
2021-04-28 Separated bolt and access holes on side panel.
    [SidePanels.scad]
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2021-05-02 X_Carriage and print head code reorganisation to use more BabyCube.
    [Parameters_CoreXY.scad, Printhead.scad, PrintheadAssemblies.scad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]
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2021-05-16 Fixed _frameBoltLength.
    [Parameters_Main.scad]
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2021-05-16 Fixed Z_MotorMount wingsize.
    [Z_MotorMount.scad]
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2021-05-17 Moved part cooling fan to other side on print head.
    [PrintheadAssemblies.scad, X_CarriageAssemblies.scad]
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2021-05-26 Added frontOffset to XY_Idler to allow slide-in front panel.
    [XY_Idler.scad]
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2021-05-26 Fixed carriage type on printhead.
    [PrintheadAssemblies.scad]
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2021-05-26 Fixed beltInset on xCarriageAssembly.
    [X_CarriageAssemblies.scad]
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2021-06-01 Fixed typo.
    [Parameters_CoreXY.scad]
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2021-06-02 Fixed test description.
    [ExtrusionCovers.scad]
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2021-06-05 Fixed wiring cover colour.
    [BaseFrontCover.scad, BasePlate.scad]
2021-06-05 Fixed heatedBedOffset for MC350.
    [PrintBed.scad]
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2021-06-05 Fixed front color explosions.
    [BasePlate.scad]
2021-06-05 Added _MGN12H suffix to printhead and x carriage.
    [PrintheadAssemblies.scad, X_CarriageAssemblies.scad]
2021-06-06 Improved handling of printhead wiring and wiring guides.
    [BackFace.scad, FaceRightExtras.scad, FaceTop.scad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]
2021-06-06 Fixed bezierTube include.
    [bezierTube.scad]
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2021-06-08 Fixed main bolts on zMotorMount.
    [Z_MotorMount.scad]
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2021-06-11 Fixed MC400 config.
    [config_MC400.scad]
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2021-06-11 Updated Y_Carriage endstop offsets to allow for different hotends.
    [Y_CarriageAssemblies.scad]
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2021-06-11 Better dual z rod handling for print bed.
    [PrintBed.scad]
2021-06-11 Fixed explosion of corkDamper for Extruder_Bracket.
    [extruderBracket.scad]
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2021-06-11 Changed to use buttonhead screw on XY_Motor_Mount brace.
    [XY_MotorMount.scad]
2021-06-11 Fixed is_true function.
    [PrintBed.scad]
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2021-06-15 Fairly big tidy of assemblies, explosions and poses to get assembly instructions into a baseline state.
    [BackFace.scad, BasePlate.scad, DisplayHousingAssemblies.scad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]
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2021-06-16 Assembly tidy: vitamin names, cable length, duplicate parts.
    [BackFace.scad, FaceLeft.scad, FaceRightExtras.scad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]
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2021-06-18 Added countersunk bolts on X_Carriage for accelerometer clearance.
    [ADXL345.scad, Base.scad, PrintheadAssemblies.scad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]
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2021-07-06 Fix useDualZMotors type.
    [Z_Rods.scad]
2021-07-06 Fixes for 350 variant.
    [BackFace.scad, FaceRight.scad, PrintBed.scad]
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2021-07-13 Fixed xRail carriage positioning.
    [X_Rail.scad]
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2021-07-13 Minor fixes.
    [EVA.scad, X_CarriageEVA.scad]
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2021-07-13 Minor fixes to X_Carriage_Belt_Attachment_MGN12H.
    [X_CarriageAssemblies.scad, X_CarriageBeltAttachment.scad]
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2021-07-14 Added tool attachment boltholes to x carriage. Improved EVA support.
    [PrintheadAssemblies.scad, X_CarriageAssemblies.scad, X_CarriageBeltAttachment.scad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]
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2021-07-15 Tidy and minor adjustments related to x carriange belt attachment.
    [X_CarriageAssemblies.scad, X_CarriageBeltAttachment.scad]
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2021-07-15 Fixed EVA naming.
    [MainAssemblyEVA.scad, X_CarriageEVA.scad]
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2021-07-16 Fixed spaces around + and -.
    [AntiBacklashNut.scad, BackFace.scad, BaseFoot.scad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]
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2021-07-16 Minor fix.
    [X_CarriageEVA.scad]
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2021-07-17 Fixed jig coloring.
    [ExtrusionDrillJig.scad, MainAssemblyJigs.scad]
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2021-07-20 Fixed numbering in assembly instructions.
    [MainAssemblies.scad]
2021-07-20 Changed Y_Carriages to allow X_Carriage belt attachment. Updated _xMin.
    [Parameters_Positions.scad, Y_CarriageAssemblies.scad]
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2021-07-21 Reduced beltAttachment size for Y_Carriage clearance.
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2021-07-25 EVA tidy and use of self tapping boltholes.
    [EVA.scad, MainAssemblyEVA.scad, X_CarriageEVA.scad]
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2021-07-25 Fixed typo in Main.scad.
    [Main.scad]
2021-07-26 Improved XY_MotorMount brace and added support for 20 idler pulleys.
    [XY_MotorMount.scad]
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2021-07-29 Added support for 4933 motor and stepdown gearing for BLDC motors.
    [CoreXYBelts.scad, XY_EncoderMount.scad, XY_MotorMount.scad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]
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2021-08-05 Fixe X_CarriageEVA includes.
    [X_CarriageEVA.scad]
2021-08-05 Fixe CoreXY test includes.
    [CoreXY.scad]
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2021-08-06 Added bolt holes for Z probe to printhead.
    [PrintheadAssemblies.scad, X_CarriageAssemblies.scad]
2021-08-06 Fixed tool changer stl coloring.
    [X_CarriageToolChanger.scad]
2021-08-06 Lessed requirement for global constants for test build.
    [PSU.scad, XY_MotorMount.scad, Z_MotorMount.scad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]
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2021-08-07 Alignment with BabyCube. Minor fixes.
    [PrintheadAssemblies.scad]
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2021-08-10 Integrated extruder bracket and IEC bracket to allow simple right side panel.
    [IEC_Housing.scad, extruderBracket.scad]
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2021-08-11 Corrected print parameter extrusion width ranges.
    [printParameters.scad]
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2021-08-16 Added lug to iec housing + code tidy.
    [IEC_Housing.scad, SidePanels.scad]
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2021-08-17 Resized topCornerPiece guide to accomodate top cover. Code tidy.
    [FaceTop.scad, TopCornerPiece.scad]
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2021-08-17 Fixed stl name.
    [SpoolHolder.scad]
2021-08-17 Reduced spoolholder bracket clearance.
    [SpoolHolder.scad]
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2021-08-18 Fixes to XY_MotorMount belt guide and color.
    [XY_MotorMount.scad]
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2021-08-31 Added support for 2060 extrusion on top face.
    [FaceTop.scad, FrameBolts.scad, config_MC300.scad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]
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2021-09-02 Printhead reorganisation and first cut of Voron Afterburner.
    [EVA.scad, MainAssemblyJubileeToolChanger.scad, MainAssemblyVoronAfterburner.scad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]
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2021-10-02 Fixed IEC housing convexity.
    [IEC_Housing.scad]
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2021-10-02 Fixed use of $exploded.
    [X_CarriageEVA.scad]
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2021-10-05 Channel nut color fixes.
    [Panels.scad]
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2021-10-06 Reduced access hole size for extrusion channel for better printing.
    [extrusionChannels.scad]
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2021-10-06 Include fix.
    [JubileeToolChanger.scad]
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2021-10-16 Don't use FaceTop wiring guide when using toolchanger.
    [FaceTop.scad]
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2021-10-17 JubileeToolChanger camelCase fix.
    [JubileeToolChanger.scad]
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2021-10-18 Markdown fix.
    [FaceLeft.scad]
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2021-10-25 Change Y_Carriages to use inserts for rail bolts.
    [Y_CarriageAssemblies.scad]
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2021-11-25 Jubilee build fix.
    [MainAssemblyJubileeToolChanger.scad, config_JubileeToolchanger.scad]
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2021-11-26 Addition of plainIdlerPulleyOffset to allow for larger pulleys.
    [CoreXYBelts.scad, Parameters_CoreXY.scad]
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2021-12-07 Changed larger variants to use 25 tooth pulleys.
    [config_MC400.scad, config_MC400KB.scad, config_MC450KB.scad]
2021-12-08 Changed fillet angle on handle to 55 degrees.
    [Handle.scad]
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2021-12-08 Corrected left brace on XY_MotorMount.
    [XY_MotorMount.scad]
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2021-12-11 Decreased _zRodOffsetY in MC300 to give better clearance for partition.
    [E20Cover.scad, config_MC300.scad]
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2021-12-16 Fixed test for including side assemblies on right side.
    [FaceRight.scad]
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2021-12-18 Fixed AccessPanel coloring.
    [AccessPanel.scad]
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2021-12-19 Moved middle bolt on heated bed to front. Adjust printbed width.
    [PrintBed.scad]
2021-12-19 Fixed typos.
    [BackFace.scad, FaceTop.scad, MainAssemblies.scad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]
2021-12-19 Improved suffixes and naming for 16 tooth variant.
    [AccessPanel.scad, FaceRight.scad, Main.scad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]
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2021-12-20 Fixed standoffs for raspberry pi.
    [BackFace.scad]
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2021-12-20 Added access holes for Z_Carriage bolts to printbed.
    [PrintBed.scad]
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2021-12-21 Fix confusion of X_Carriage extraX and extraOverlap.
    [X_CarriageAssemblies.scad]
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2021-12-21 Alignment with BabyCube beltSize and beltSeparation parameterisation. Uniqueification of xCarriageFrontSizeM and xCarriageBackSizeM functions.
    [PrintheadAssemblies.scad, X_CarriageAssemblies.scad, X_CarriageEVA.scad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]
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2021-12-21 Renaming of X_Carriage sides to belt and hotend side.
    [Printhead.scad, PrintheadAssemblies.scad, X_Carriage.scad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]
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2021-12-22 Support for HC and non-HC forms of X_Carriage.
    [PrintheadAssemblies.scad, X_CarriageAssemblies.scad]
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2021-12-24 Better parameterisation of X_Carriage and handling of halfCarriage.
    [FaceTop.scad, MainAssemblies.scad, Parameters_CoreXY.scad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]
2021-12-24 Configuration fixes.
    [FaceRight.scad, MainAssemblyDualZRods.scad, MainAssemblyKinematicBed.scad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]
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2021-12-27 Grammer correction.
    [FaceTop.scad]
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2021-12-27 JubileeToolChanger build fix.
    [JubileeToolChanger.scad]
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2021-12-28 Kinematic bed build fix.
    [JubileeKinematicBed.scad, Z_Rods.scad]
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2021-12-28 Z_Carriage rename to avoid clash with BabyCube.
    [Printbed.scad]
2021-12-29 Added tolerance to Z_MotorMount motor bolt holes. Also improved filleting.
    [Z_MotorMount.scad]
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2021-12-30 Fixed capitalisation and commented out unused code.
    [IEC_Housing.scad]
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2021-12-30 Removed new features from NIUGUY_CB_PSU pending NopSCADlib changes.
    [psus.scad]
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2022-01-02 Markdown fixes.
    [Main.scad, MainAssemblies.scad]
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2022-01-05 Improved partion panel and connection to motor mounts.
    [AccessPanel.scad, IEC_Housing.scad, XY_MotorMount.scad]
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2022-01-06 Inverted Z_Carriages for 235 sized printbed.
    [E20Cover.scad, Parameters_Main.scad, Z_Carriage.scad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]
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2022-01-09 Fixed gap position in belts.
    [CoreXY.scad, CoreXYBelts.scad]
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2022-01-12 IEC housing cutout fix.
    [IEC_Housing.scad]
2022-01-13 Fixes to Z motor mount for kinematic.
    [Z_MotorMount.scad]
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2022-01-13 Fixed whitespace in assembly instructions.
    [MainAssemblies.scad]
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2022-01-22 XChange build fixes.
    [MainAssemblyXChange.scad, X_CarriageAssemblies.scad, X_CarriageXChange.scad]
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2022-01-26 Reversed xyMotorMountBrace orientation indicator.
    [XY_MotorMount.scad]
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2022-01-28 First working cut of reversed belts.
    [CoreXYReversed.scad, Parameters_CoreXY.scad, XY_MotorMount.scad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]
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2022-01-28 XY_Idler support for reversed belts.
    [XY_Idler.scad]
2022-01-28 Further reversed belts support.
    [CoreXYBelts.scad, Parameters_CoreXY.scad]
2022-01-28 Add reversed belts hardware to XY_MotorMount.
    [XY_MotorMount.scad]
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2022-01-29 Improved reversed belt support.
    [XY_MotorMount.scad, X_CarriageAssemblies.scad, Y_CarriageAssemblies.scad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]
2022-01-29 Fixed fillet height on xyMotorMountBlock.
    [XY_MotorMount.scad]
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2022-01-29 Fixed XChange_assembly name.
    [MainAssemblyXChange.scad]
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2022-01-31 Fixed carriage position for XChange assembly.
    [MainAssemblyXChange.scad]
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2022-01-31 Changed MC350 to use reversed belts.
    [config_MC350.scad]
2022-01-31 Increased bearing clearances and front offset on XY_Idler.
    [XY_Idler.scad]
2022-01-31 Added tolerance for XY_MotorMount brace.
    [XY_MotorMount.scad]
2022-01-31 Fixed variant string.
    [config_MC300RB.scad]
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2022-01-31 MC400 and MC450 config changed to use reverse belts.
    [config_MC400.scad, config_MC450.scad]
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2022-02-01 Comment fix.
    [X_CarriageXChange.scad]
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2022-02-01 Fixed XY_Motor_Mount spacer diameter.
    [XY_MotorMount.scad]
2022-02-01 Changed Voron adaptors to use reversed belts.
    [config_Voron_Afterburner.scad, config_Voron_Mini_Afterburner.scad]
2022-02-02 Updated configs to use reversed belts.
    [config_JubileeToolchanger.scad, config_KinematicBed.scad, config_MC400.scad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]
2022-02-02 xRail no longer hides carriage when $hide_rails is set.
    [X_Rail.scad]
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2022-02-02 Updated JubileeToolChanger build. Removed FaceTop from BOM. Moved stlimport directory outside of MaybeCube.
    [FaceTop.scad, JubileeToolChanger.scad, MainAssemblyJubileeToolChanger.scad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]
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2022-02-03 JubilleeKinematic import fix.
    [JubileeKinematicBed.scad]
2022-02-04 Added tolerance to XY_MotorMount boss radius.
    [XY_MotorMount.scad]
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2022-02-22 Fixed explosion artefact.
    [FaceTop.scad]
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2022-02-24 Fixed XY_Motor_Mount_Pulley_Spacer colour.
    [XY_MotorMount.scad]
2022-03-27 EVA positioning and explosion fixes.
    [EVA.scad, MainAssemblyEVA.scad, X_CarriageEVA.scad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]
2022-05-17 Fixed bolthole radii on XY_Ider.
    [XY_Idler.scad]
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2022-05-23 Increased clearance for extruder motor under XY_MotorMount.
    [Parameters_CoreXY.scad]
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2022-05-31 Increased clearances for spoolholder.
    [SpoolHolder.scad]
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2022-06-12 Corrected side panel boltholes for spoolholder.
    [FaceRight.scad, FaceRightExtras.scad, Panels.scad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]
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2022-06-22 Fixes for mdlint.
    [FaceLeft.scad, Main.scad, Printbed.scad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]
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2022-06-23 Corrected access hole positions.
    [BackFace.scad, FaceRight.scad]
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2022-07-02 Fix up bolts and bolt holes on faceTopFront.
    [FaceTop.scad]
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2022-07-02 Added clearance around IEC housing for wiring.
    [IEC_Housing.scad, extruderBracket.scad]
2022-07-02 Jigs build fixes.
    [E20ThreadTappingJig.scad, MainAssemblyJigs.scad, PanelJig.scad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]
2022-07-02 Eva build fixes.
    [MainAssemblyEVA_2_4_2.scad]
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2022-07-03 Kinematic bed fix.
    [Printbed.scad]
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2022-07-03 Build fixes.
    [AccessPanel.scad, IEC_Housing.scad]
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2022-07-03 Fixes to bolts for pcb on base.
    [BasePlate.scad, pcbs.scad]
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2022-07-04 Fixes to and additional motors for >= 400 size variants.
    [FaceRight.scad, Panels.scad, Z_MotorMount.scad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]
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2022-07-05 EVA_MC_mgn12_bottom_horns_fi_stl name fix.
    [X_CarriageEVA.scad]
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
